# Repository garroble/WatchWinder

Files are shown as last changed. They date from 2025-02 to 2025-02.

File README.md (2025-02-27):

# WatchWinder
## About the project
3D Printed Watch Winder controlled through Arduino IoT Cloud.

A watch winder is a machine that rotates an automatic mechanical watch to keep it on time and date.

Depending on the watch, it needs to rotate several hundreds times a day. Some of them need to rotate clockwise and some counterclockwise. Others can rotate in either direction.

With this watch winder, the watch is always on time, keeping it running and preserving it from breakdowns during prolonged shutdowns.

In the project you can find everything needed to build your own watch winder.

## Mechanics
On the mechanics folder you will find the 3D model designed in FreeCAD so you can make any changes needed for your watch.
The watch winder has been designed considering watch bracelets up to 26mm width.
The FreeCAD model also includes an assembly to check how everything fits together. (Under development)

You can also find the STL files en m3f files to directly import the parts in 3D printing slicing programs.
The models have been proved on Bambu Lab A1 mini printer successfully.

The 3D model is also published on:
* Maker World (https://makerworld.com/es/models/1157015-watch-winder#profileId-1162305)

Other parts that need to be purchased to get the full mechanical assembly are:

mBOM (Mechanical Parts):

| ID | Part name | Part number | Quantity |
|----|---|---|---|
| S1 | Spring | 0.5x5x25 | 2 |
| M1 | Stepper Motor | 28BYJ-48 | 1 |
| I1 | Insert M3 | M3x0.5 5.74mm length | 2 |
| I2 | Insert M4 | M4x0.7 8.15mm length | 2 |
| S2 | Screw | M3x10 | 2 |
| S3 | Screw | M4x20 | 2 |
| B1 | Bearing | 608zz | 2 |
| C1 | Cable F-F | Dupont Cable FF | 10 |
| DC | Barrel Plug | DC Barrel Plug to cable | 1 |

eBOM (Electronic Parts):

| ID | Part name | Part number | Quantity |
|---|---|---|---|
| PCB1 | Arduino | Nano RP2040 | 1 |
| PCB2 | Motro Driver | ULN2003 | 1 |
| PCB3 | Voltage Step Down | MP1584EN | 1 |
| DC | DC Wall Adapater  | 12V 500mA adapter compatible with DC barrel | 1 |

### Assembly
1. Place the M3 inserts on the Body with a soldering iron for the motor.
2. Place the M4 inserts on the Body with a soldering iron for the bearrings.
3. Place the 608zz and bearring stopper on the hole and fix it with the M4x20 screw.
4. Place the drum inside of the body.
5. Place the motor on the rear part of the body fitting the shaft inside of the drum.
6. Fix the motor to the body with M3x10 screws.
7. Place all PCB boards in place.
8. Cut 4 Dupont Cable in one end, two for DC power supply and two for DC ground.
9. Connect the DC power supply cables to barrel + signal.
10. Connect the DC ground cables to barrel - signal.
11. Ensure the polarity by connecting the DC Wall adapater and measuring the voltage wiht a multimeter.
12. Connect one DC power supply cable and one DC ground cable to Arduino Nano Vin and GND signals.
13. Connect the other DC power supply cable and the other DC ground cable to MP1584EN board in V+ and V-.
14. Use two dupont cables to connect the MP1584EN output Vout+ and Vout- to ULN2003 power input Vin and GND.
15. Connect Arduino Nano pins 7, 8, 9, 10 to IN1, IN2, IN3, IN4 on ULN2003 board.
16. Connect the Stepper Motor to the ULN2003 board.
17. Install front and rear covers on the body.
18. Place the springs on Watch Press front shafts.
19. Insert Watch Press Front shafts on Watch Press Rear.
20. Place the wath on Wath Press and insert it on the Watch Winder drum.

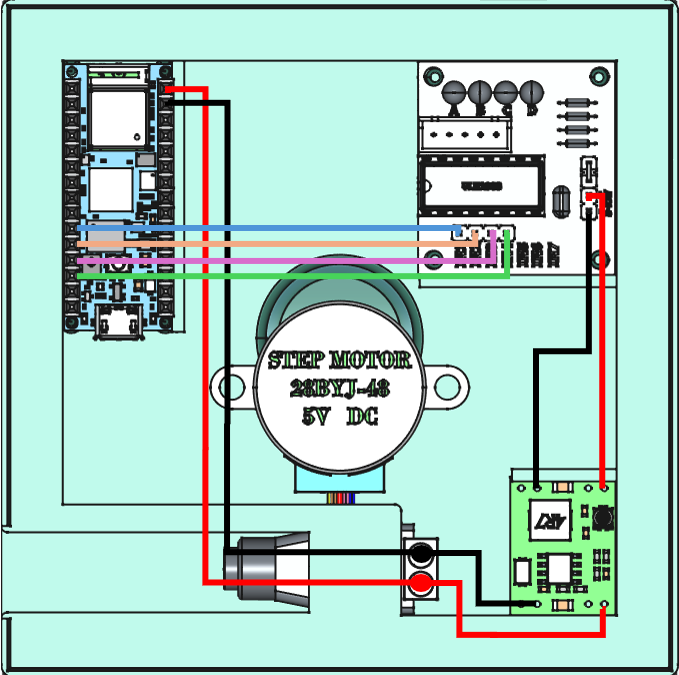
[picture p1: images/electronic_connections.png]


## Firmware
The firmware has been developed on Arduino IDE 2.3.4 (https://www.arduino.cc/en/software) and Arduino Cloud (https://app.arduino.cc/) 

On Arduino Cloud:
1. Include the Arduino Nano board as a new Device.
2. Under Things, include the following variables to the Device:
   1. cl_winder_status as Boolean, Read Only and update on change.
   2. cl_winder_turns as Counter, Read Only and update on change.
   3. ctrl_start_time as CloudSchedule, Read & Write and update on change.
   4. ctrl_switch as Boolean, Read & Write and update on change.
3. This will generate the basic Sketch with all the variables and callbacks ready to be used. The thingProperties.h shall be very similar to the one published here.
4. Follow the published code to get your Watch Winder ready and running.
5. Create a Dashboard in Arduino Cloud to control and get the status of your winder:
   1. Switch linked to ctrl_switch to turn it on/off any time.
   2. LED linked to cl_winder_status to check if it is running.
   3. Scheduler linked to ctrl_start_time to schedule the start time, duration and repeat every.
   4. Graph linked to cl_winder_turns to keep track of the number of rotations.

### Firmware tuning
Based on your watch, you may need to change the number of rotations a day needed.
You can set it on the WatchWinder.ino file:
> #define WATCH_TURNS_PER_DAY 750

The program continuously rotates clockwise as it is. If you need to make it rotate counterclockwise, just remove the minus signal on:
> int motor_target = -MOTOR_MAX_STEPS;

## License
Licensed under GNU General Public License V3.0.

## Acknowledgements
Thanks to the following sites and their community for providing the 3D models for all the purchased parts.
* 3D Content Central. https://www.3dcontentcentral.com/
* GrabCAD. https://grabcad.com/

Thanks for the amazing AccelStepper library for Arduino. It is extremely easy to make it work and it has some really cool features.
* AccelStepper: https://www.airspayce.com/mikem/arduino/AccelStepper/

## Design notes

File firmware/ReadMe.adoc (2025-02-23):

:Author: garroble
:Email:
:Date: 10/02/2025
:Revision: 1.0
:License: Public Domain

= Project: WatchWinder

A custom made Watch Winder based on Arduino Cloud and 3D printing.

== Step 1: Installation
Go to https://github.com/garroble/WatchWinder for more information.

== Step 2: Arduino Cloud setup.
Create the following Cloud Variables:
....
Things Setup
  ├── bool          cl_winder_status => Cloud status of the device to know if it is running.
  ├── CloudCounter  cl_winder_turns  => Number of complete turns done in an active period.
  ├── CloudSchedule ctrl_start_time  => Scheduler to setup the daily active period.
  └── bool          ctrl_switch      => Remote control on/off.
....

=== Folder structure

....
 Firmware                  => Arduino sketch folder
  ├── WatchWinderCloud.ino => main Arduino file
  ├── thingProperties.h    => header file for ArduinoIoTCloud
  ├── arduino_secrets.h    => header for WiFi SSID/PASS
  └── ReadMe.adoc          => this file
....

=== Help
This document is written in the _AsciiDoc_ format, a markup language to describe documents. 
If you need help you can search the http://www.methods.co.nz/asciidoc[AsciiDoc homepage]
or consult the http://powerman.name/doc/asciidoc[AsciiDoc cheatsheet]

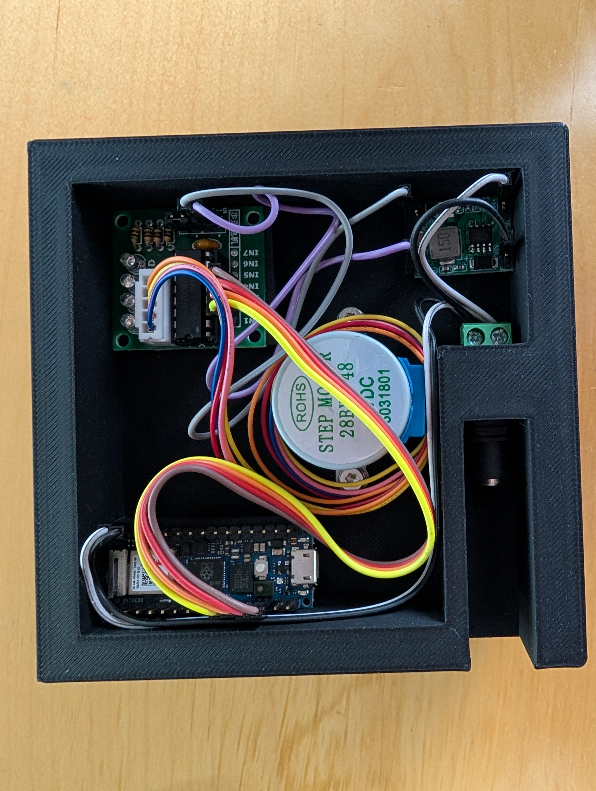
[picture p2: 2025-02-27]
images/watch_winder_electronics.jpg

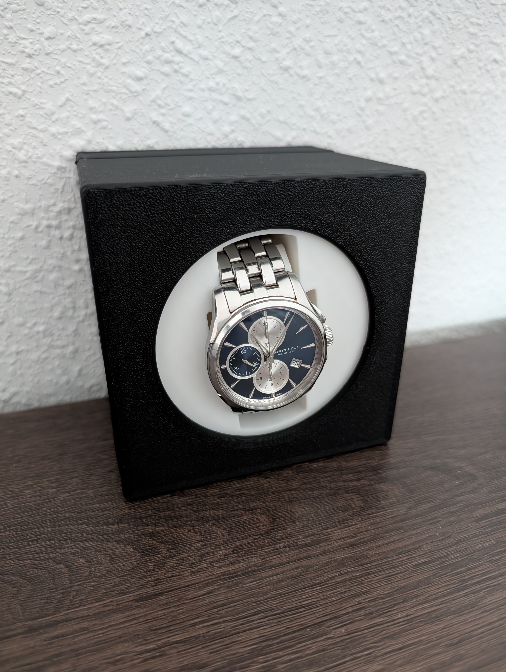
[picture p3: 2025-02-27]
images/watch_winder.jpg

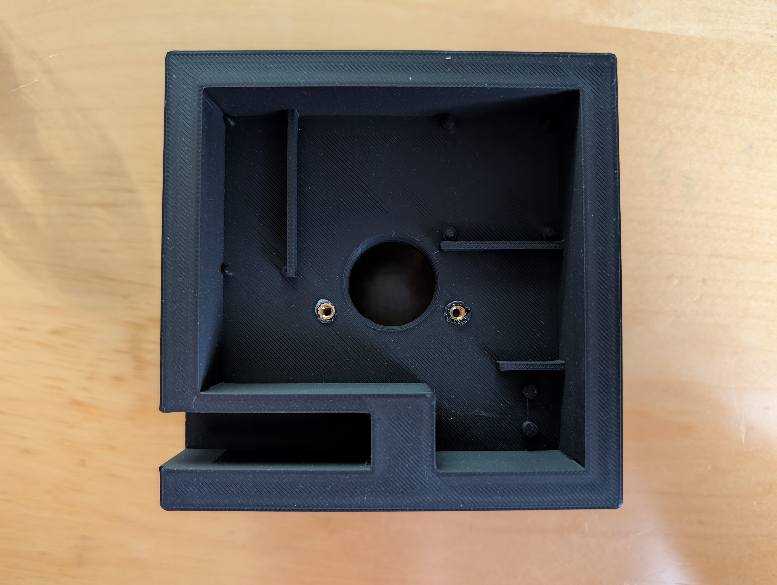
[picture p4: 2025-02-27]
images/watch_winder_body.jpg

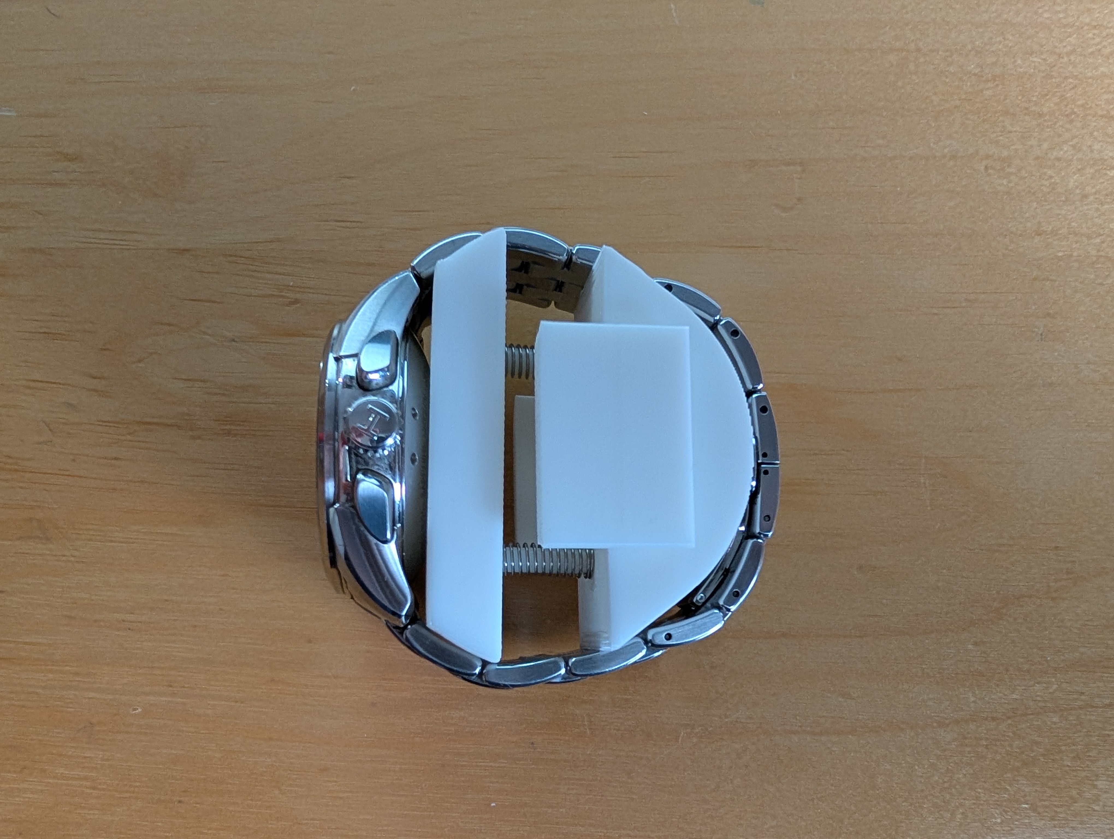
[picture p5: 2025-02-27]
images/watch_winder_press_watch.jpg

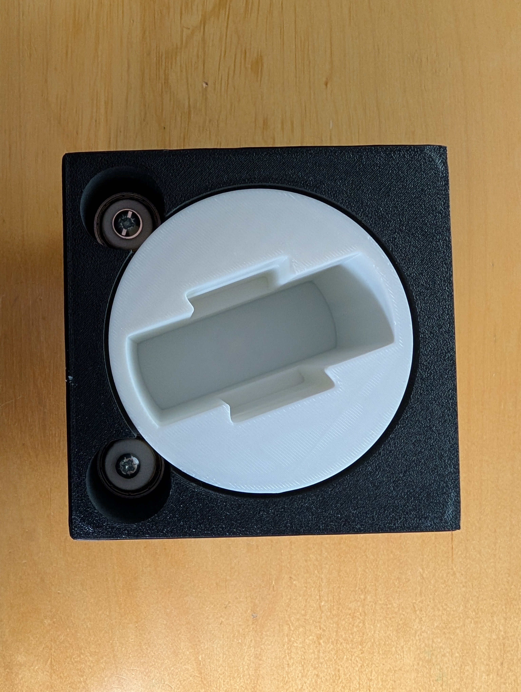
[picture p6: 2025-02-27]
images/watch_winder_drum.jpg

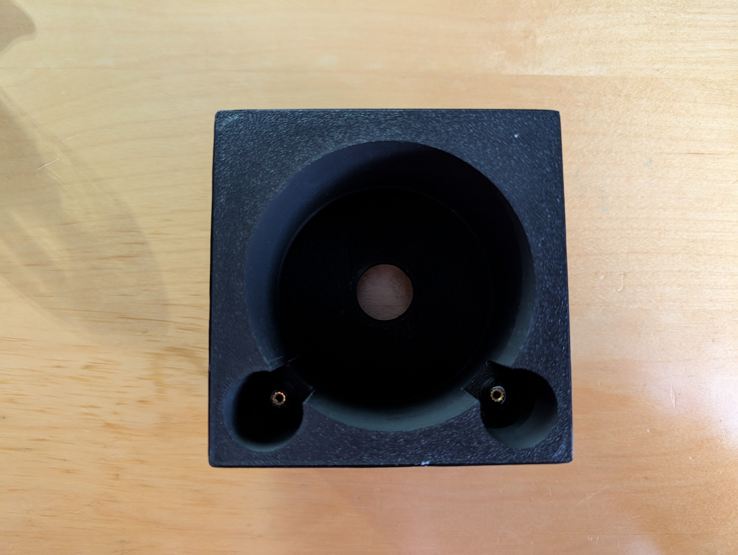
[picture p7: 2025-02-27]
images/watch_winder_body_front.jpg

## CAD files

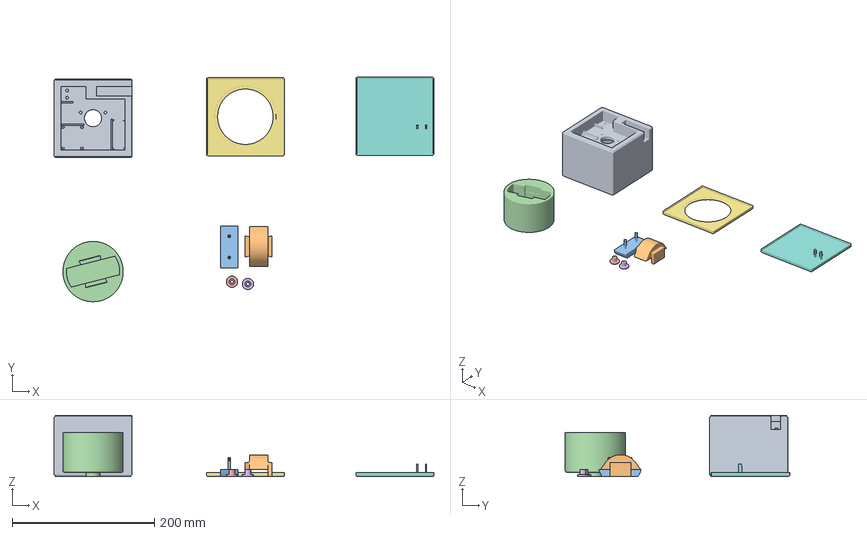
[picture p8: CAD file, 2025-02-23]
mechanics/3mf/Watch_Winder.3mf
535.2 x 316.3 x 86.0 mm
Watch_Winder-Body.stl
Watch_Press_Rear.stl
Watch_Press_Front.stl
Watch_Winder-Drum.stl
Bearing_Stopper.stl x 2
Watch_Winder-Front_Cover.stl
Watch_Winder-Rear_Cover.stl

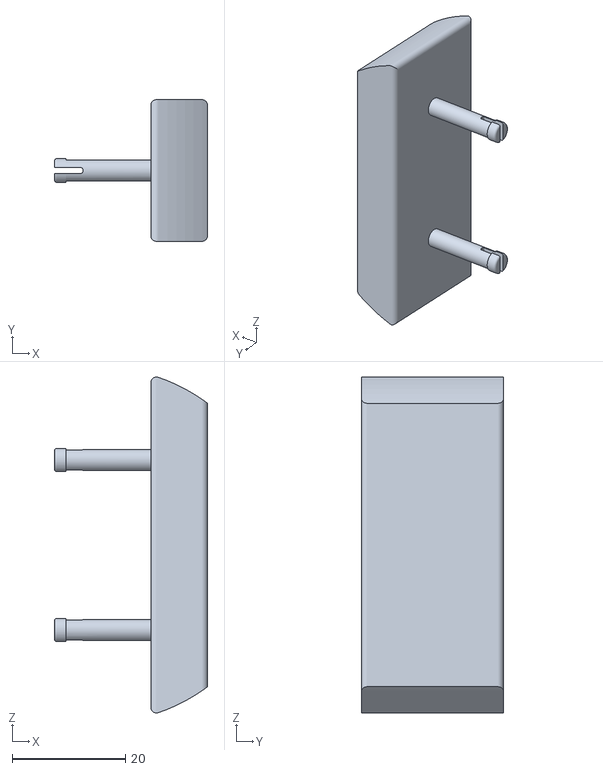
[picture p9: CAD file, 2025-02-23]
mechanics/stl/Watch_Press_Front.stl
27.0 x 25.0 x 59.3

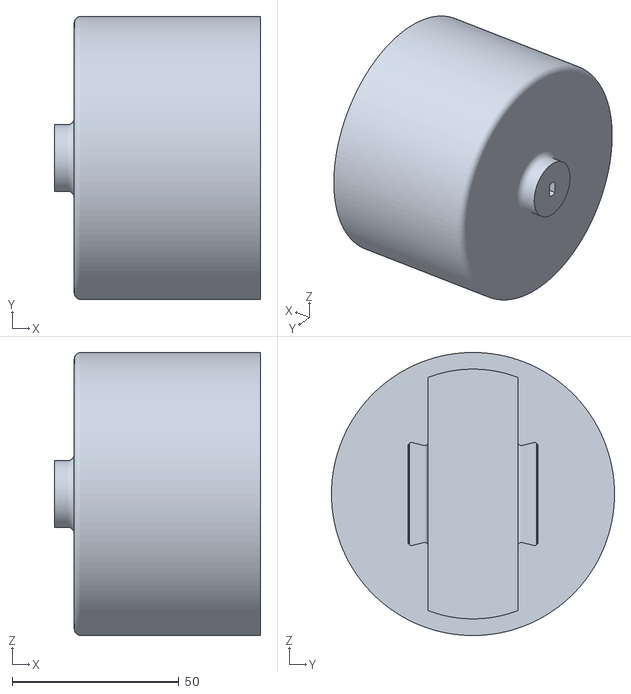
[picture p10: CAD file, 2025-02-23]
mechanics/stl/Watch_Winder-Drum.stl
62.0 x 85.0 x 85.0

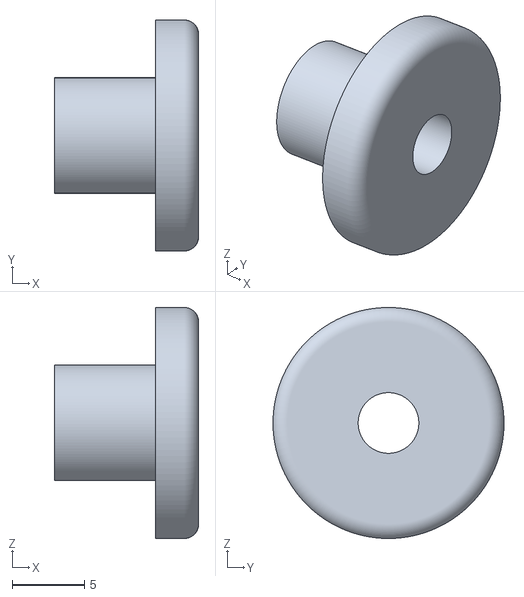
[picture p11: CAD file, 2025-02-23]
mechanics/stl/Bearing_Stopper.stl
10.0 x 16.0 x 16.0

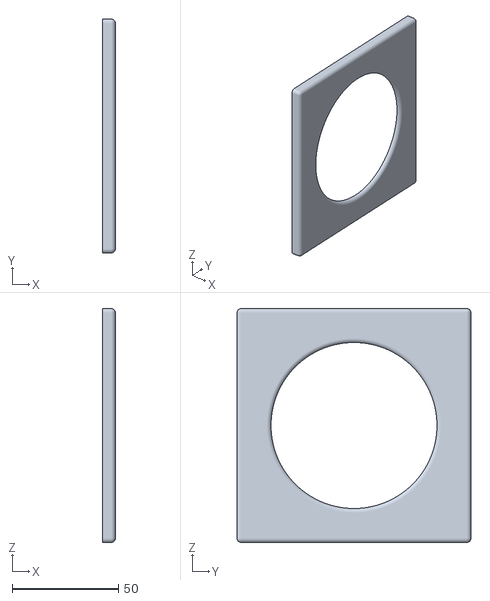
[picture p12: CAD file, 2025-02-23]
mechanics/stl/Watch_Winder-Front_Cover.stl
6.00 x 110.0 x 110.0

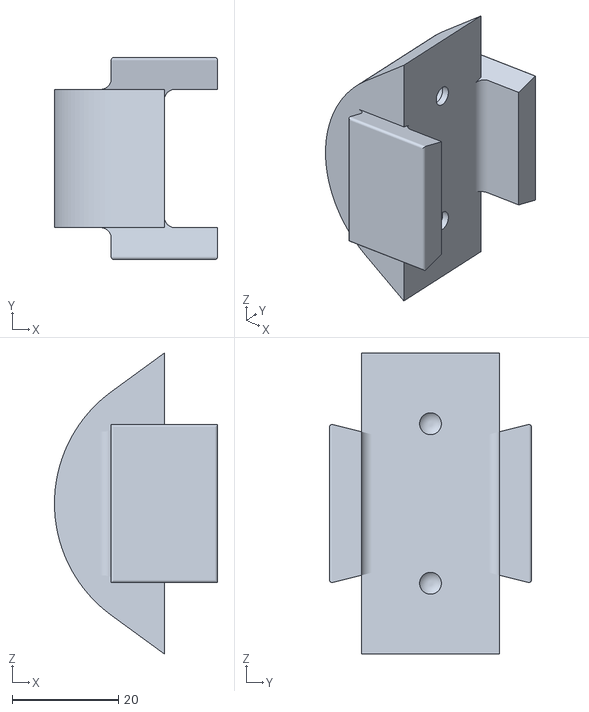
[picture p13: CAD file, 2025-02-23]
mechanics/stl/Watch_Press_Rear.stl
30.7 x 38.0 x 56.6

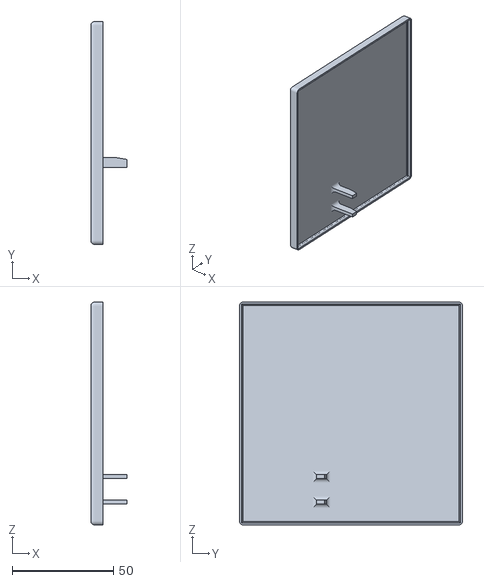
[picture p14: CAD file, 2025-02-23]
mechanics/stl/Watch_Winder-Rear_Cover.stl
18.0 x 110.0 x 110.0

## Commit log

2025-02-15 First upload.
    First working version.
    Program the schedule from Arduino IoT Cloud Dashboard.
    Auto calculate time interval based on required turns.
2025-02-23 Include mechanics and readme.
    [Bearing_Stopper.stl, Watch_Press_Front.stl, Watch_Press_Rear.stl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]
2026-02-06 Solve stepper motor in stop active mode in some cases at the end of the working period.
2026-05-23 Include arduino_secrets.h which is removed in cloud version.
